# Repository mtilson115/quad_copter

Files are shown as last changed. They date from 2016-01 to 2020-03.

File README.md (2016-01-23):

quad_copter
===========

Microchip PIC32MX795F512L With uCOS RTOS and Accel Gyro driver port from arduino

**Compiling**

1. Install the xc32 compiler from microchip
2. Modify Makefile to point CC to the to where the compiler is located
3. type make

**Output Files**

A binary (same as a .elf) and a .hex file will be placed in the BIN directory

**Modifying what is included in the build**

In side Makefile, you can modify the DIRS variable to include new folders to compile.

**Required directory structure**

If you do add new folders to the build, you must use the ./src and ./inc file naming structure for the
build system to work.

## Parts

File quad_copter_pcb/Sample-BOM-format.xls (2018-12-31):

This is a sample BOM for online BOM pricing system. Please use this preferred format for your BOM that you upload.
Note: DNI applies to whole row. If only some specific locations of a given ITEM are not to be installed, please create two rows for that item and mark one as DNI.
BOM: <Board Name Here>
Assembly Part Number/Revision:
Customer / Company Name:
Item # | Quantity per board | Manufacturer Part # | Do Not Install | Reference designators | Vendor (optional) | Vendor Part Number (optional) | Value (optional) | Size / Footprint (optional) | Part description/ specs (optional, but recommended) | Manfacturer (optional)
1 | 58 | ECJ-0EB1E103K |  | C1,C2,C3,C4,C5,C6,C7,C8,C9,C10,C21,C22,C23,C24,C25,C26,C33,C34,C35,C36,C37,C38,C39,C40,C41,C42,C43,C44,C45,C46,C47,C48,C69,C70,C71,C72,C73,C74,C75,C76,C77,C78,C79,C80,C81,C82,C83,C84,C85,C86,C87,C88,C89,C90,C91,C92,C121,C122 | Digi-Key | PCC2270CT-ND | 0.01uF | C0402 | CAP .01UF 25V CERAMIC X7R 0402 | Panasonic
2 | 2 | T520L337M2R5ATE025 |  | C12,C15 | Digi-Key | 399-5134-1-ND | 330uF | C6032 | CAP TANT 330UF 2.5V 20% SMD | Kemet
3 | 2 | T520L337M2R5ATE025 | DNI | C16,C17 | Digi-Key | 399-5134-1-ND | 330uF | C6032 | CAP TANT 330UF 2.5V 20% SMD | Kemet
4 | 6 | ECJ-2FB1E475M |  | C29,C30,C31,C32,C59,C60 | Digi-Key | PCC2321CT-ND | 4.7uF | C0805 | CAP CERAMIC 4.7UF 25V X5R 0805 | Panasonic
5 | 32 | GRM155F51E104ZA01D |  | C61,C62,C63,C64,C93,C94,C95,C96,C97,C98,C99,C100,C101,C102,C103,C104,C105,C106,C107,C108,C109,C110,C111,C112,C113,C114,C115,C116,C125,C126,C127,C128 | Digi-Key | 490-3271-1-ND | 0.1uF | C0402 | CAP CER .1UF 25V Y5V 0402 | Murata
6 | 10 | C3225X7R1E106M | DNI | C65,C66,C67,C68,C119,C120, C147,C158,C170,C171 | Mouser | 810-C3225X7R1E106M | 10uF | C1210 (3225 metric) | CAP CER 10uF 25V X7R 20% SMD 1210 | TDK
7 | 2 | ECJ-2FF1H105Z |  | C146,C156 | Digi-Key | PCC2404CT-ND | 1uF | C0805 | CAP CERAMIC 1UF 50V F 0805 | Panasonic
8 | 3 | C0805C103K5RACTU |  | C149,C151,C161 | Digi-Key | 399-1158-1-ND | 10nF | C0805 | CAP 10000PF 50V CERAMIC X7R 0805 | KEMET
9 | 3 | LMK325BJ476MM-T |  | C167, C169, C141 | Digi-Key | 587-1383-1-ND | 47uF | C1210 (3225 metric) | CAP CER 47UF 10V X5R 1210 | Taiyo Yuden
10 | 3 | C3216X5R1A106M |  | C139,C142,C174 | Digi-Key | 445-1387-1-ND | 10uF | C1206 (3216 metric) | CAP CER 10UF 10V X5R 20% 1206 | Panasonic
11 | 5 | CC0805KRX7R9BB104 |  | C159, C152, C162, C166, C168 | Digi-Key | 311-1140-1-ND | 0.1uF | C0805 | CAP .10UF 50V CERAMIC X7R 0805 | Yageo
12 | 1 | T495D477M006ATE045 |  | C153 | Digi-Key | 399-5220-1-ND | 470uF | C7343-31 | CAP TANTALUM 470UF 6.3V 0.045ohm ESR SMD | Kemet
13 | 5 | ECJ-2VB1H102K |  | C154,C148,C157,C160,C150 | Digi-Key | PCC102BNCT-ND | 1000pF | c0805 | CAP 1000pF 50V CERAMIC X7R 0805 | Panasonic
14 | 2 | C3216X5R0J476M |  | C163,C164 | Digi-Key | 445-1428-1-ND | 47uF | c1206 (3216 metric) | CAP CER 47UF 6.3V X5R 20% 1206 | TDK
15 | 2 | B540C-13-F |  | D1,D2 | Digi-Key | B540C-FDICT-ND | 40V 5A | SMC | DIODE SCHOTTKY 40V 5A SMC | Diodes Inc
16 | 12 | APHCM2012CGCK-F01 |  | D3,D4,D5,D6,D7,D8,D9,D10,D11,D12,D13,D14 | Digi-Key | 754-1094-1-ND | LED | LED0805 | LED 2X1.25MM LOPRO 570NM GRN SMD | Kingbright Corp
17 | 2 | 12226-8250-00FR | DNI | J1,J4 | Mouser | 517-12226-825000FR | 12226-8250-00FR | CONN_SMD-26 | CONN SDR 26POS R/A RECEPT SMD | 3M
18 | 1 | 141-0701-201 |  | J2 | Mouser | 530-141-0701-201 | SMA-VERT | CON_SMA_V_TH | SMA Connector STR PC MNT JACK RECPT STAINLESS STEEL | Emerson
19 | 1 | 2-5177986-5 |  | J5 | Digi-Key | A35089CT-ND | CON120 | conn_2x60_th | CONN PLUG 120 POS VERT DUAL | TE Connectivity
20 | 6 | 961103-6404-AR |  | J6,J7,J8,J9,J15,J17 | Digi-Key | 3M9448-ND | CON3 | HDR1X3_TH | CONN HEADER VERT SGL 3POS GOLD | 3M
21 | 1 | 87831-1420 |  | J10 | Digi-Key | WM17469-ND | 87831-1420 | conn_2x7th | CONN HEADER 14POS 2MM VERT GOLD | Molex
22 | 2 | ASP-134488-01 |  | J11,J12 | Samtec Inc | ASP-134488-01 | ASP-134488-01 | SMD_50x8_BGA | CONN SNGL-END ARRAY MALE 400POS | Samtec Inc
23 | 1 | 961102-6404-AR |  | J16 | Digi-Key | 3M9447-ND | JUMPER | HDR1X2TH | CONN HEADER VERT SGL 2POS GOLD | 3M
24 | 25 | GBC36SFBN-M30 |  | JP1-JP25 | Digi-Key | S1043E-36-ND | 1 PIN HEADER | HDR1x1 | 1 PIN HEADER; BREAK FROM 36 PIN STANDARD HEADER STRIP | Sullins
25 | 3 | MPZ2012S601A |  | L1,L2,L3 | Digi-Key | 445-2206-1-ND | INDUCTOR | ind_0805 | FERRITE CHIP BEAD 600 OHM SMD | TDK
26 | 3 | MSS1048-103MLB |  | L4,L6,L7 | COILCRAFT | MSS1048-103MLB | 10uH | ind_Mss1048 | INDUCTOR POWER 10UH 4.0A SMD 26mOHM | COILCRAFT
27 | 1 | SRR1260-120M |  | L5 | Arrow | SRR1260-120M | 12uH | ind_Srr1260 | INDUCTOR POWER 12UH 5.0A SMD 23mOHM | BOURNS
28 | 1 | SRR6603-1R5ML |  | L8 | Digi-Key | SRR6603-1R5MLCT-ND | 1.5uH | ind_Srr6603 | INDUCTOR POWER 1.5UH 2.8A SMD 45mOHM | BOURNS
29 | 6 | ERJ-2GEJ271X |  | R1,R2,R3,R4,R5,R6 | Digi-Key | P270JCT-ND | 270R | R0402 | RES 270 OHM 1/10W 5% 0402 SMD | Panasonic
30 | 3 | ERJ-2GEJ331X |  | R7,R8,R9 | Digi-Key | P330JCT-ND | 330 | R0402 | RES 330 OHM 1/10W 5% 0402 SMD | Panasonic
31 | 7 | ERJ-2GEJ472X |  | R10,R11,R21,R22,R23,R24,R25 | Digi-Key | P4.7KJCT-ND | 4.7K | R0402 | RES 4.7K OHM 1/10W 5% 0402 SMD | Panasonic
32 | 12 | RC0402JR-0710KL |  | R26,R27,R28,R42,R43,R44, R50,R51,R52,R53,R54,R55 | Digi-Key | 311-10KJRCT-ND | 10K | R0402 | RES 10K OHM 1/16W 5% 0402 SMD | Panasonic
33 | 2 | ERJ-6ENF6192V |  | R12,R15 | Digi-Key | P61.9KCCT-ND | 61.9K | R0805 | RES 61.9K OHM 1/8W 1% 0805 SMD | Panasonic
34 | 1 | ERJ-6ENF1581V |  | R13 | Digi-Key | P1.58KCCT-ND | 1.58K | R0805 | RES 1.58K OHM 1/8W 1% 0805 SMD | Panasonic
35 | 7 | ERJ-6ENF1001V |  | R14,R17,R20,R34,R35,R36,R40 | Digi-Key | P1.00KCCT-ND | 1K | R0805 | RES 1.00K OHM 1/8W 1% 0805 SMD | Panasonic
36 | 1 | ERJ-6ENF2871V |  | R16 | Digi-Key | P2.87KCCT-ND | 2.87K | R0805 | RES 2.87K OHM 1/8W 1% 0805 SMD | Panasonic
37 | 1 | ERJ-6ENF2492V | DNI | R18 | Digi-Key | P24.9KCCT-ND | 24.9K | R0805 | RES 24.9K OHM 1/8W 1% 0805 SMD | Panasonic
38 | 1 | ERJ-6ENF2550V |  | R19 | Digi-Key | P255CCT-ND | 255 | R0805 | RES 255 OHM 1/8W 1% 0805 SMD | Panasonic
39 | 7 | RC0603JR-07100RL |  | R29,R30,R31,R32,R33,R48,R49 | Digi-Key | 311-100GRCT-ND | 100 | R0603 | RES 100 OHM 1/10W 5% 0603 SMD | Panasonic
40 | 4 | ERJ-3GEY0R00V |  | R37,R45,R46,R47 | Digi-Key | P0.0GCT-ND | 0 | R0603 | RES ZERO OHM 1/10W 5% 0603 SMD | Panasonic
41 | 2 | PTS645VL31 LFS |  | SW1,SW2 | Digi-Key | CKN9094-ND | PTS645VL31 LFS | sw_tact_6mm_th | SWITCH TACT R/A 6MM H=3.15MM, Through Hole, Right Angle | C&K Components
42 | 2 | SN74ALVC244NSR |  | U1,U7 | Digi-Key | 296-12863-1-ND | SN74ALVC244 | SOP-20 | IC BUFF/DVR TRI-ST OCTAL 20SOP | Texas Instruments
43 | 2 | XCF32PVOG48C |  | U2,U8 | Digi-Key | 122-1458-ND | XCF32PVOG48C | TSOP-48 | IC PROM SRL 1.8V 32M GATE 48TSOP | Xilinx
44 | 2 | XC5VLX110-3FFG1760C |  | U3,U6 | Nu Horizons | XC5VLX110-3FFG1760C | XC5VLX110-3FFG1760C | BGA-1760 | IC FPGA VIRTEX-5 110K 1760FBGA | Xilinx
45 | 2 | LM22670TJE-ADJ/NOPB |  | U4,U5 | Digi-Key | LM22670TJE-ADJCT-ND | LM22670TJE-ADJ/NOPB | TO263-7 | IC REG SWITCH BUC 3A ADJ TO263-7 | Texas Instruments
46 | 2 | LM3102MH/NOPB |  | U9,U11 | Newark | 54M4671 | LM3102MH/NOPB | TSSOP-20 | IC REG SYNC BUCK 42V2.5A 20TSSOP | Texas Instruments
47 | 1 | SN65LVDS179DGK | DNI | U13 | Digi-Key | 296-6918-5-ND | SN65LVDS179DGK | MSOP-8 | IC HS DIFF LINE DRVR/RCVR 8-MSOP | Texas Instruments
48 | 1 | CSX750FBC-20.000M-UT |  | U14 | Mouser | 695-CSX750FBC-20 | CSX-750FBC-20Mhz | OSC_CSX750 | OSC 3.3V PROG CMOS OE 100PPM 20MHZ | Citizen
END OF BOM

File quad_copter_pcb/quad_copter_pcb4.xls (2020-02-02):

This is a sample BOM for online BOM pricing system. Please use this preferred format for your BOM that you upload.
Note: DNI applies to whole row. If only some specific locations of a given ITEM are not to be installed, please create two rows for that item and mark one as DNI.
BOM: Quad Copter
Assembly Part Number/Revision: 00000002
Customer / Company Name: Mitchell Tilson
Item # | Quantity per board | Manufacturer Part # | Do Not Install | Reference designators | Vendor (optional) | Vendor Part Number (optional) | Value (optional) | Size / Footprint (optional) | Part description/ specs (optional, but recommended) | Manfacturer (optional)
1 | 1 | CL21A106KOQNNNE |  | C1 | Digi-Key | 1276-1096-2-ND | 10uF | c0805 | CAP CER 10UF 16V X5R 0805 | Samsung Electro-Mechanics
2 | 1 | TAJA226M010RNJ |  | C2 | Digi-Key | 478-5798-1-ND | 22uF | c1206 | 22µF Molded Tantalum Capacitors 10V 1206 (3216 Metric) 3 Ohm | AVX
3 | 2 | 06031A250GAT2A |  | C4,C5 | Digi-Key | 478-10197-2-ND | 26pF | c0603 | 25pF ±2% 100V Ceramic Capacitor C0G, NP0 0603 (1608 Metric) | AVX
4 | 7 | CL10F104ZO8NNNC |  | C9,C10,C8,C7,C11,C13,C12 | Digi-Key | 1276-1258-6-ND | 0.1uF | c0603 | CAP CER 0.1UF 16V Y5V 0603 | Samsung Electro-Mechanics
5 | 1 | CL10A106MQ8NNNC |  | C6 | Digi-Key | 1276-1119-1-ND | 10uF | c0603 | CAP CER 10UF 6.3V X5R 0603 | Samsung Electro-Mechanics
6 | 2 | 06033A150JAT2A |  | C14,C15 | Digi-Key | 478-10804-2-ND | 15pF | c0603 | CAP CER 15PF 25V C0G/NP0 0603 | AVX
7 | 3 | SML-LX1206GW-TR |  | D3,D2,D1 | Digi-Key | 67-1002-1-ND |  | led1206 | LED GREEN DIFFUSED 1206 SMD | Lumex Opto/Components Inc.
8 | 1 | 10103594-0001LF |  | J12 | Digi-Key | 609-4050-1-ND |  |  | CONN RCPT USB2.0 MICRO B SMD R/A | Amphenol FCI
9 | 1 | 317-87-121-41-005101 |  | JP2 | Digi-Key | 1212-1133-ND |  | pitch: 0.070" (1.78mm) | PCB SKT, 21 POLE | Preci-Dip
10 | 1 | RJ11-6N-B |  | JP1 | Digi-Key | CCM1394-ND |  |  | CONN MOD JACK 6P6C R/A UNSHLD | TE Connectivity Corcom Filters
11 | 3 | RR1220P-103-D |  | R4,R6,R2 | Digi-Key | RR12P10.0KDTR-ND | 10k | r0805 | RES SMD 10K OHM 0.5% 1/10W 0805 | Susumu
12 | 3 | RMCF0805JT56R0 |  | R9,R8,R1 | Digi-Key | RMCF0805JT56R0DKR-ND | 56 | r0805 | RES 56 OHM 5% 1/8W 0805 | Stackpole Electronics Inc.
13 | 2 | CR0603-JW-471ELF |  | R5,R7 | Digi-Key | CR0603-JW-471ELFCT-ND | 470 | r0603 | RES SMD 470 OHM 5% 1/10W 0603 | Bourns Inc.
14 | 1 | RC0805FR-072K8L |  | R3 | Digi-Key | 311-2.80KCRTR-ND | 2.8k | r0805 | RES SMD 2.8K OHM 1% 1/8W 0805 | Yageo
15 | 2 | RR1220P-242-D |  | R12,R13 | Digi-Key | RR12P2.4KDTR-ND | 2.4k | r0805 | RES SMD 2.4K OHM 0.5% 1/10W 0805 | Susumu
16 | 1 | RNCS0805BKE10R0 |  | R14 | Digi-Key | RNCS0805BKE10R0TR-ND | 10 | r0805 | RES 10 OHM 0.1% 1/10W 0805 | Stackpole Electronics Inc.
17 | 2 | RS-187R05A2-DS MT RT |  | S1,S2 | Digi-Key | CKN10361TR-ND |  | TACTILE_SWITCH_SMD_5.2MM | SWITCH TACTILE SPST-NO 0.05A 12V | C&K
18 | 1 | PIC32MX795F512L-80I/PT |  | U4 | Digi-Key | PIC32MX795F512L-80I/PT-ND |  | TQFP-100_12x12mm_P0.4mm | IC MCU 32BIT 512KB FLASH 100TQFP | Microchip Technology
19 | 1 | LT1085CM-3.3#PBF |  | U1 | Digi-Key | LT1085CM-3.3#PBF-ND | 3.3V |  | IC REG LINEAR 3.3V 3A D2PAK-3 | Linear Technology/Analog Devices
20 | 1 | PPTC081LFBN-RC |  | U3 | Digi-Key | S7006-ND | CONN8 | .1’’ pitch | CONN HEADER FEMALE 8POS .1" TIN | Sullins Connector Solutions
21 | 1 | CM200C32768HZFT |  | Y2 | Digi-Key | 300-8742-1-ND | 32kHz | Crystal_SMD_7050-4Pin_7.0x5.0mm | CRYSTAL 32.7680KHZ 12.5PF SMD | Citizen Finedevice Co Ltd
22 | 1 | 9C-8.000MEEJ-T |  | Y1 | Digi-Key | 887-1263-2-ND | 8MHz | HC49UP | CRYSTAL 8.0000MHZ 18PF SMD | TXC CORPORATION
END OF BOM

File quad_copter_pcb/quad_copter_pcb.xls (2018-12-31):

Title | Quad Copter
Revision | 1
Date | Sat 08 Dec 2018 03:06:19 PM PST
Generated | Sat 08 Dec 2018 03:06:19 PM PST
Company | Self
Comment 1
Comment 2
Comment 3
Comment 4
Total Parts | 64
Total Unique Parts | 32
Ref | Qty | Value | Footprint | Field4 | Part Reference | Notes
C1 | 1 | C_10uF | Capacitor_SMD:C_0805_2012Metric_Pad1.15x1.40mm_HandSolder |  | https://www.digikey.com/product-detail/en/tdk-corporation/C2012JB1V106M085AC/445-11518-6-ND/3957614 | Please order and solder in
C2 | 1 | C_22uF | Capacitor_SMD:C_1206_3216Metric_Pad1.42x1.75mm_HandSolder |  | https://www.digikey.com/product-detail/en/avx-corporation/TAJA226M010RNJ/478-5798-1-ND/2136389 | Please order and solder in
C5 C4 | 2 | C26pF | Capacitor_SMD:C_0603_1608Metric_Pad1.05x0.95mm_HandSolder |  | https://www.digikey.com/product-detail/en/avx-corporation/06031A250GAT2A/478-10197-2-ND/1598435 | Please order and solder in
C9 C10 | 2 | C_.1uF | Capacitor_SMD:C_0603_1608Metric_Pad1.05x0.95mm_HandSolder |  | https://www.digikey.com/product-detail/en/samsung-electro-mechanics/CL10F104ZO8NNNC/1276-1258-6-ND/3891772 | Please order and solder in
C6 | 1 | C10uF | Capacitor_SMD:C_0603_1608Metric_Pad1.05x0.95mm_HandSolder |  | https://www.digikey.com/product-detail/en/tdk-corporation/C1608X5R0J106M080AB/445-4112-2-ND/1975459 | Please order and solder in
C8 C7 C11 C13 C12 | 5 | C.1uF | Capacitor_SMD:C_0603_1608Metric_Pad1.05x0.95mm_HandSolder |  | https://www.digikey.com/product-detail/en/samsung-electro-mechanics/CL10F104ZO8NNNC/1276-1258-6-ND/3891772 | Please order and solder in
C15 C14 | 2 | C15pF | Capacitor_SMD:C_0603_1608Metric_Pad1.05x0.95mm_HandSolder |  | https://www.digikey.com/product-detail/en/avx-corporation/06033A150JAT2A/478-10804-2-ND/1599104 | Please order and solder in
D3 D2 D1 | 3 | LED | LED_SMD:LED_1206_3216Metric_Pad1.42x1.75mm_HandSolder |  | https://www.digikey.com/product-detail/en/lumex-opto-components-inc/SML-LXFT1206SGD-TR/SML-LXFT1206SGD-TR-ND/7364535 | Please order and solder in
H1 H2 H3 H4 H5 H6 H7 H8 H9 H10 | 10 | MountingHole_Pad | MountingHole:MountingHole_2.5mm_Pad |  |  | I have this already
H11 H13 H12 H_4 | 4 | MountingHole | MountingHole:MountingHole_3.2mm_M3 |  |  | I have this already
J4 J3 J2 J1 | 4 | Conn_01x03_Male | Connector_PinHeader_2.54mm:PinHeader_1x03_P2.54mm_Vertical |  |  | I have this already
J5 | 1 | Conn_02x05_Odd_Even | Connector_PinHeader_2.54mm:PinHeader_2x05_P2.54mm_Vertical |  |  | I have this already
J6 J9 | 2 | Conn_02x02_Odd_Even | Connector_PinHeader_2.54mm:PinHeader_2x02_P2.54mm_Vertical |  |  | I have this already
J7 J11 | 2 | Conn_01x05 | Connector_PinHeader_2.54mm:PinHeader_1x05_P2.54mm_Vertical |  |  | I have this already
J8 | 1 | Conn_02x04_Odd_Even | Connector_PinHeader_2.54mm:PinHeader_2x04_P2.54mm_Vertical |  |  | I have this already
J12 | 1 | USB_B_Micro | Connector_USB:USB_Micro-B_Amphenol_10103594-0001LF_Horizontal |  | https://www.digikey.com/product-detail/en/amphenol-fci/10103594-0001LF/609-4050-1-ND/2350357 | Please order and solder in
J10 | 1 | Conn_02x03_Odd_Even | Connector_PinHeader_2.54mm:PinHeader_2x03_P2.54mm_Vertical |  |  | I have this already
JP2 | 1 | XBEE LEAVE EMPTY | RF:XBEE | S6B | https://www.digikey.com/product-detail/en/preci-dip/317-87-121-41-005101/1212-1133-ND/3757383 | Please order. I will solder this one in. If part is unavailable, don’t hold up order.
JP1 | 1 | RJ11-6 | Connectors:RJ11-6 | CONN-08590 | https://www.digikey.com/product-detail/en/te-connectivity-corcom-filters/RJ11-6N-B/CCM1394-ND/260247 | Please order and solder in
R4 R6 | 2 | R10k | Resistor_SMD:R_0805_2012Metric_Pad1.15x1.40mm_HandSolder |  | https://www.digikey.com/product-detail/en/susumu/RR1220P-103-D/RR12P10.0KDTR-ND/432315 | Please order and solder in
R9 R8 R1 | 3 | R_56 | Resistor_SMD:R_0805_2012Metric_Pad1.15x1.40mm_HandSolder |  | https://www.digikey.com/product-detail/en/stackpole-electronics-inc/RMCF0805JT56R0/RMCF0805JT56R0DKR-ND/2427421 | Please order and solder in
R5 R7 | 2 | R470 | Resistor_SMD:R_0603_1608Metric_Pad1.05x0.95mm_HandSolder |  | https://www.digikey.com/product-detail/en/bourns-inc/CR0603-JW-471ELF/CR0603-JW-471ELFCT-ND/3740990 | Please order and solder in
R2 | 1 | R10K | Resistor_SMD:R_0805_2012Metric_Pad1.15x1.40mm_HandSolder |  | https://www.digikey.com/product-detail/en/susumu/RR1220P-103-D/RR12P10.0KDTR-ND/432315 | Please order and solder in
R3 | 1 | R2.8k | Resistor_SMD:R_0805_2012Metric_Pad1.15x1.40mm_HandSolder |  | https://www.digikey.com/product-detail/en/yageo/RC0805FR-072K8L/311-2.80KCRTR-ND/727711 | Please order and solder in
R12 R13 | 2 | R2.4k | Resistor_SMD:R_0805_2012Metric_Pad1.15x1.40mm_HandSolder |  | https://www.digikey.com/product-detail/en/susumu/RR1220P-242-D/RR12P2.4KDTR-ND/432300 | Please order and solder in
R14 | 1 | R10 | Resistor_SMD:R_0805_2012Metric_Pad1.15x1.40mm_HandSolder |  | https://www.digikey.com/product-detail/en/stackpole-electronics-inc/RNCS0805BKE10R0/RNCS0805BKE10R0TR-ND/1800064 | Please order and solder in
S1 S2 | 2 | MOMENTARY-SWITCH-SPST-2-SMD-5.2MM | Switches:TACTILE_SWITCH_SMD_5.2MM | SWCH-08247 | https://www.digikey.com/product-detail/en/c-k/RS-187R05A2-DS-MT-RT/CKN10361TR-ND/2747186 | Please order and solder in
U4 | 1 | PIC32MX795F512L-X_PT | Package_QFP:TQFP-100_12x12mm_P0.4mm |  | https://www.microchip.com/wwwproducts/en/PIC32MX795F512L | Please order and solder in. Seriously, I can’t solder this.
U1 | 1 | LT1085-3.3 | Package_TO_SOT_SMD:TO-263-3_TabPin2 |  | http://cds.linear.com/docs/en/datasheet/1083ffe.pdf | Please order and solder in
U3 | 1 | accel_gyro_conn | Connector_PinSocket_2.54mm:PinSocket_1x08_P2.54mm_Vertical |  | https://www.digikey.com/product-detail/en/sullins-connector-solutions/PPTC081LFBN-RC/S7006-ND/810147 | Please order. I will solder this one in.
Y2 | 1 | Crystal_GND23 | Crystal:Crystal_SMD_7050-4Pin_7.0x5.0mm |  | https://www.digikey.com/product-detail/en/citizen-finedevice-co-ltd/CM200C32768HZFT/300-8742-1-ND/2108134 | Please order and solder in
Y1 | 1 | Crystal_8MHz | Clocks:HC49UP |  | https://www.digikey.com/product-detail/en/txc-corporation/9C-8.000MEEJ-T/887-1263-2-ND/2207683 | Please order and solder in
BOM made with KICAD_BOM_WIZARD (https://github.com/HashDefineElectronics/KiCad_BOM_Wizard.git)
Generated Sat 08 Dec 2018 03:06:19 PM PST

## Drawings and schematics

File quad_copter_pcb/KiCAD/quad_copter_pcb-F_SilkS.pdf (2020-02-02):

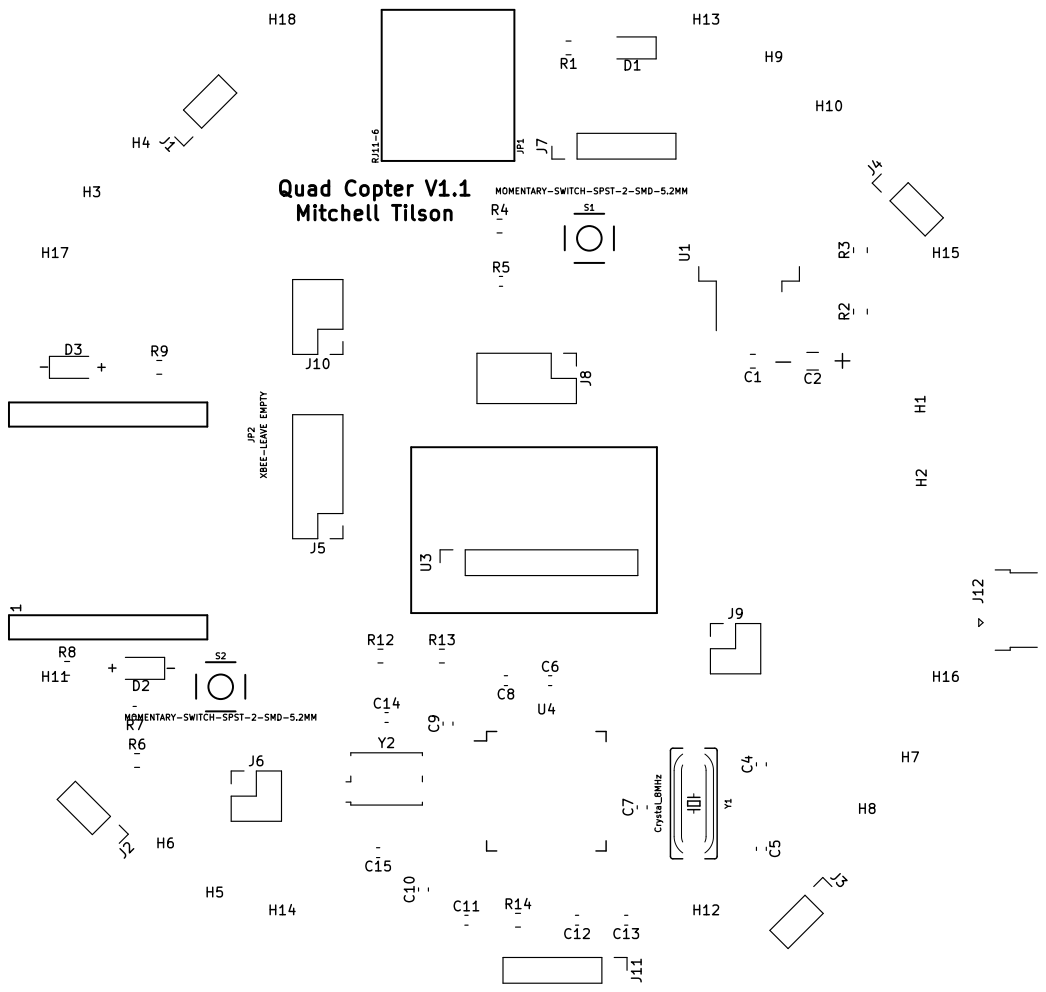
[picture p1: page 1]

Quad Copter V1.1 Mitchell Tilson

S1 MOMENTARY-SWITCH-SPST-2-SMD-5.2MM

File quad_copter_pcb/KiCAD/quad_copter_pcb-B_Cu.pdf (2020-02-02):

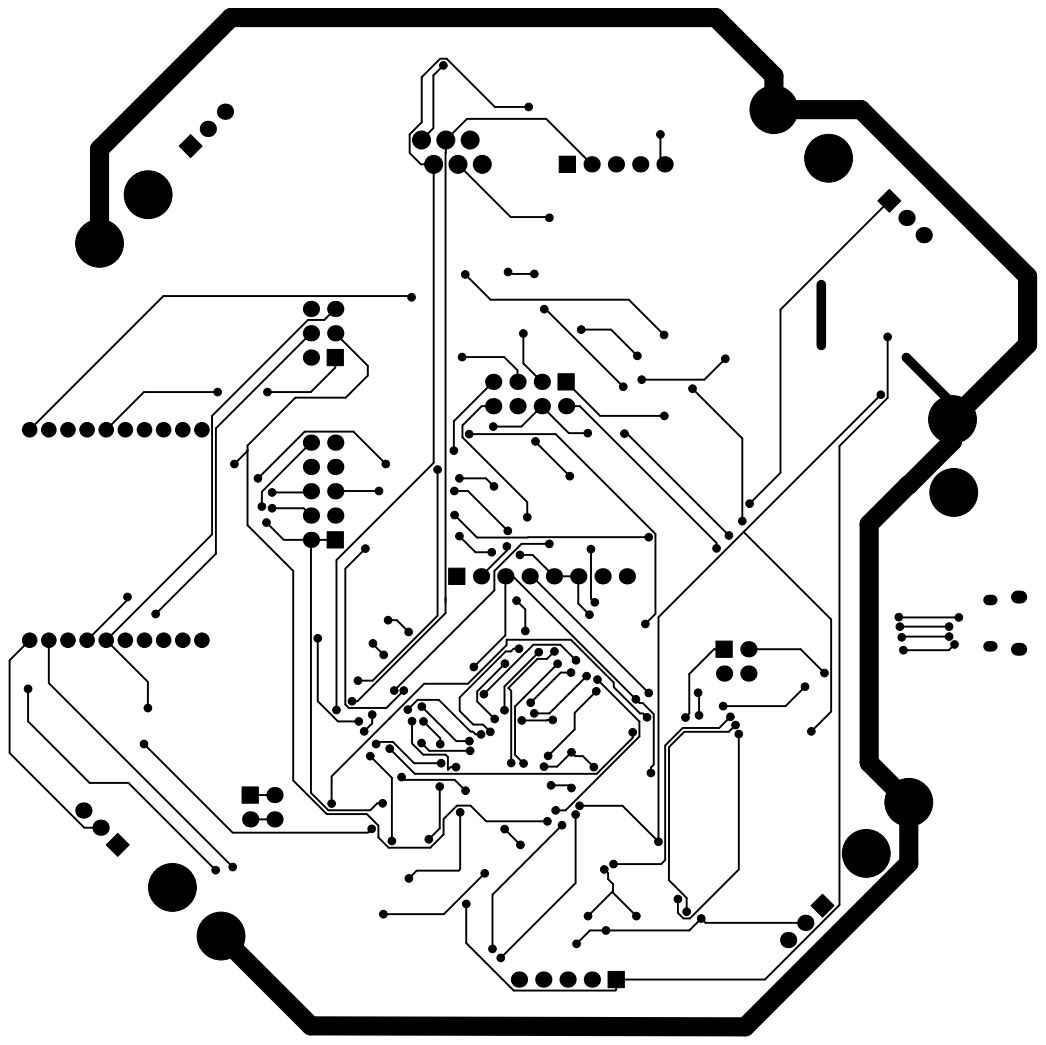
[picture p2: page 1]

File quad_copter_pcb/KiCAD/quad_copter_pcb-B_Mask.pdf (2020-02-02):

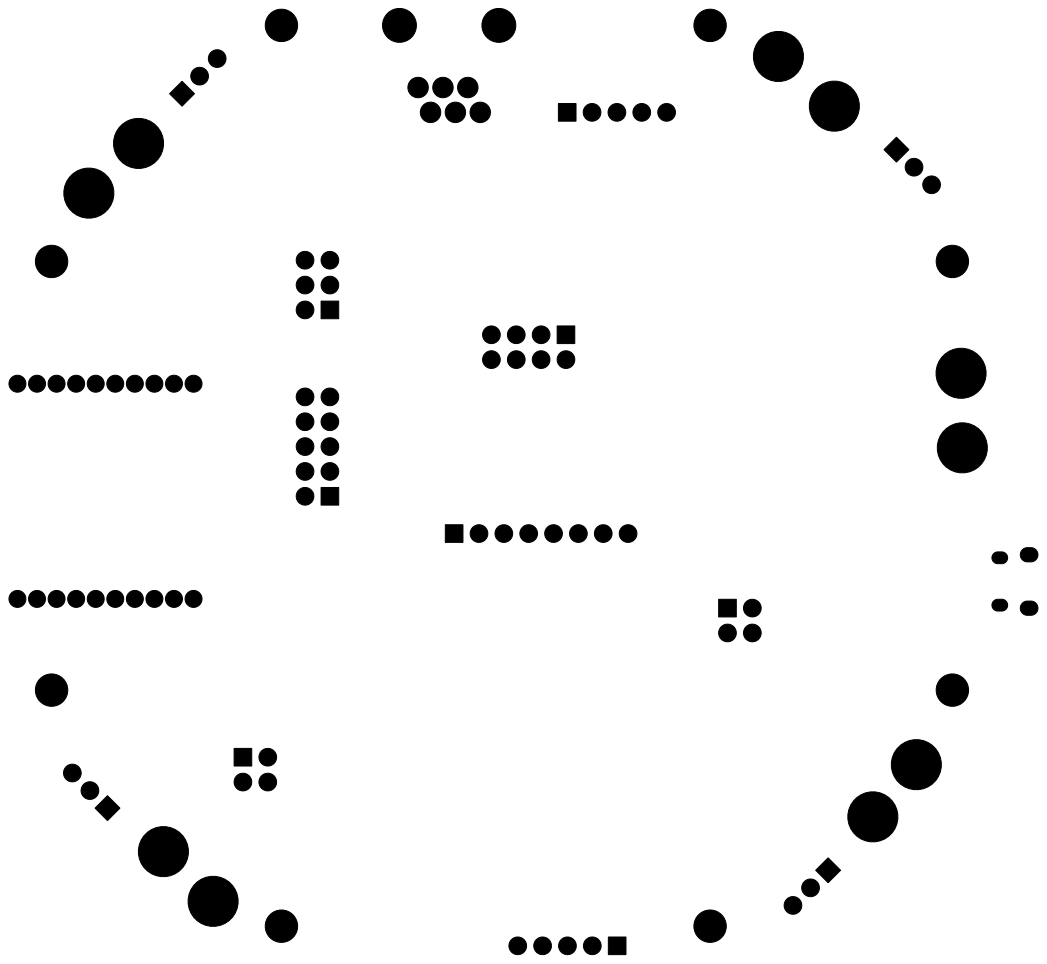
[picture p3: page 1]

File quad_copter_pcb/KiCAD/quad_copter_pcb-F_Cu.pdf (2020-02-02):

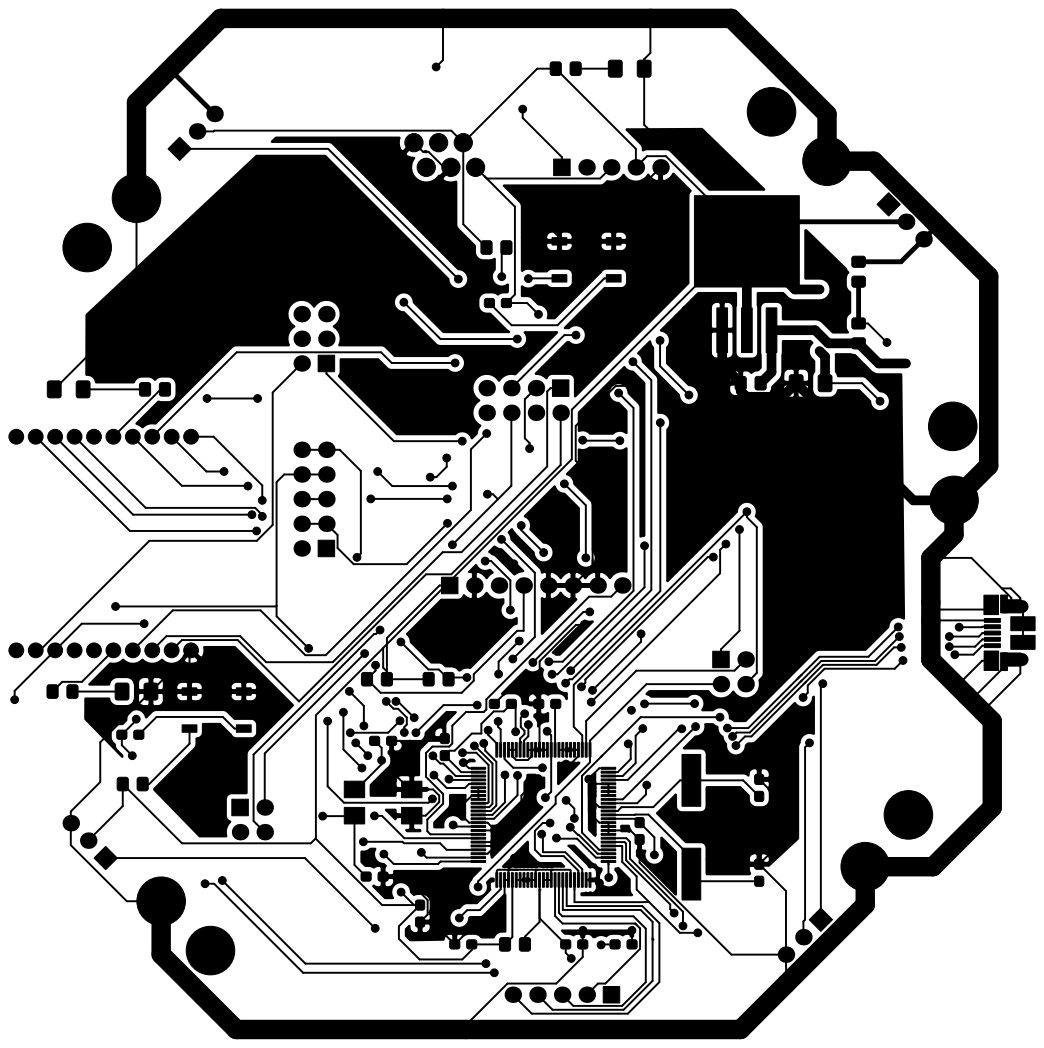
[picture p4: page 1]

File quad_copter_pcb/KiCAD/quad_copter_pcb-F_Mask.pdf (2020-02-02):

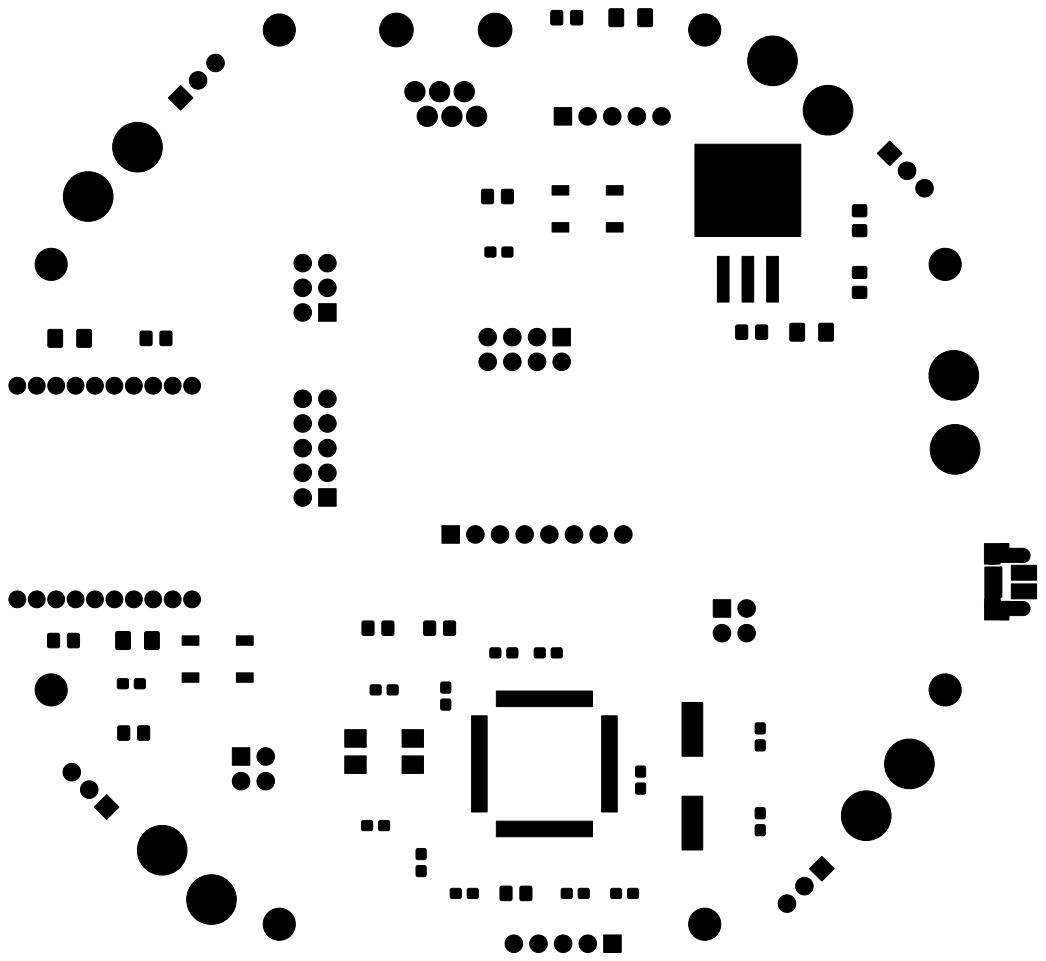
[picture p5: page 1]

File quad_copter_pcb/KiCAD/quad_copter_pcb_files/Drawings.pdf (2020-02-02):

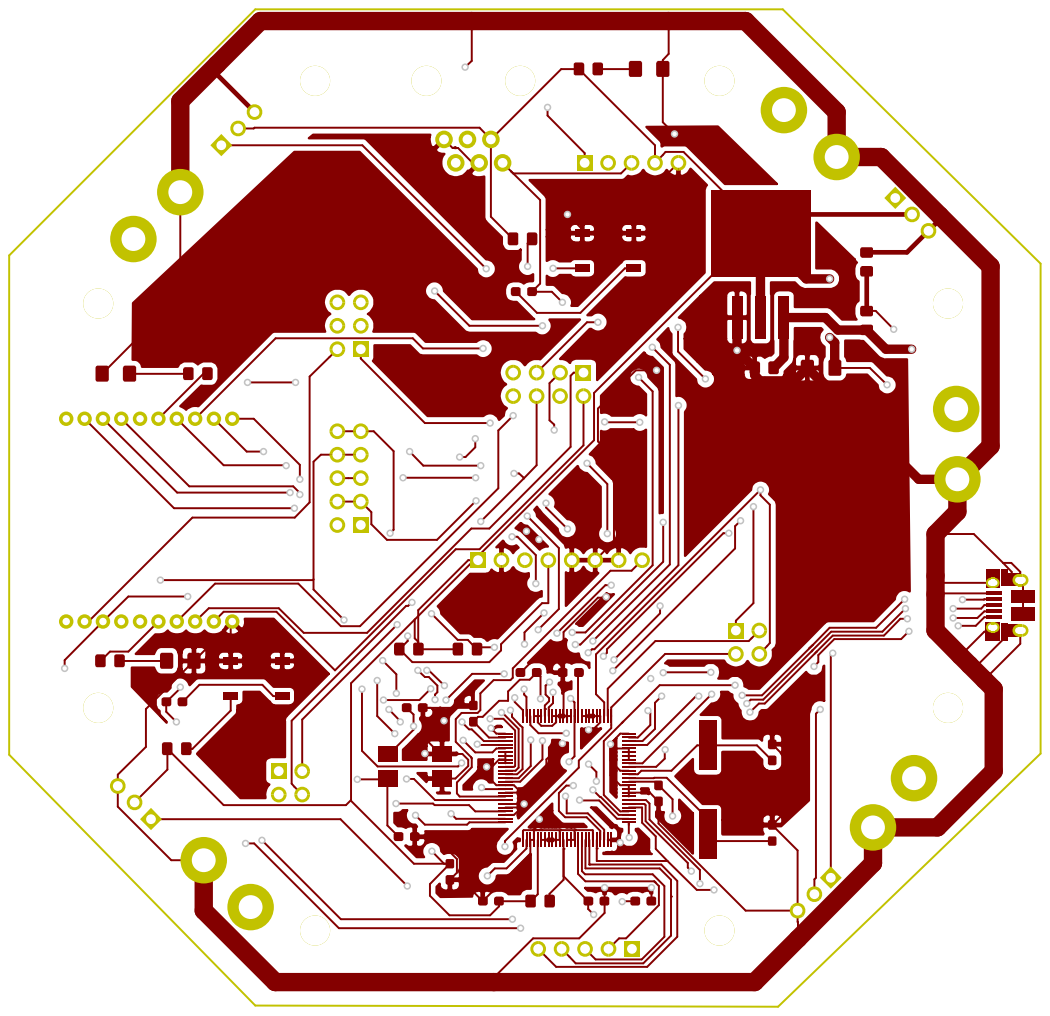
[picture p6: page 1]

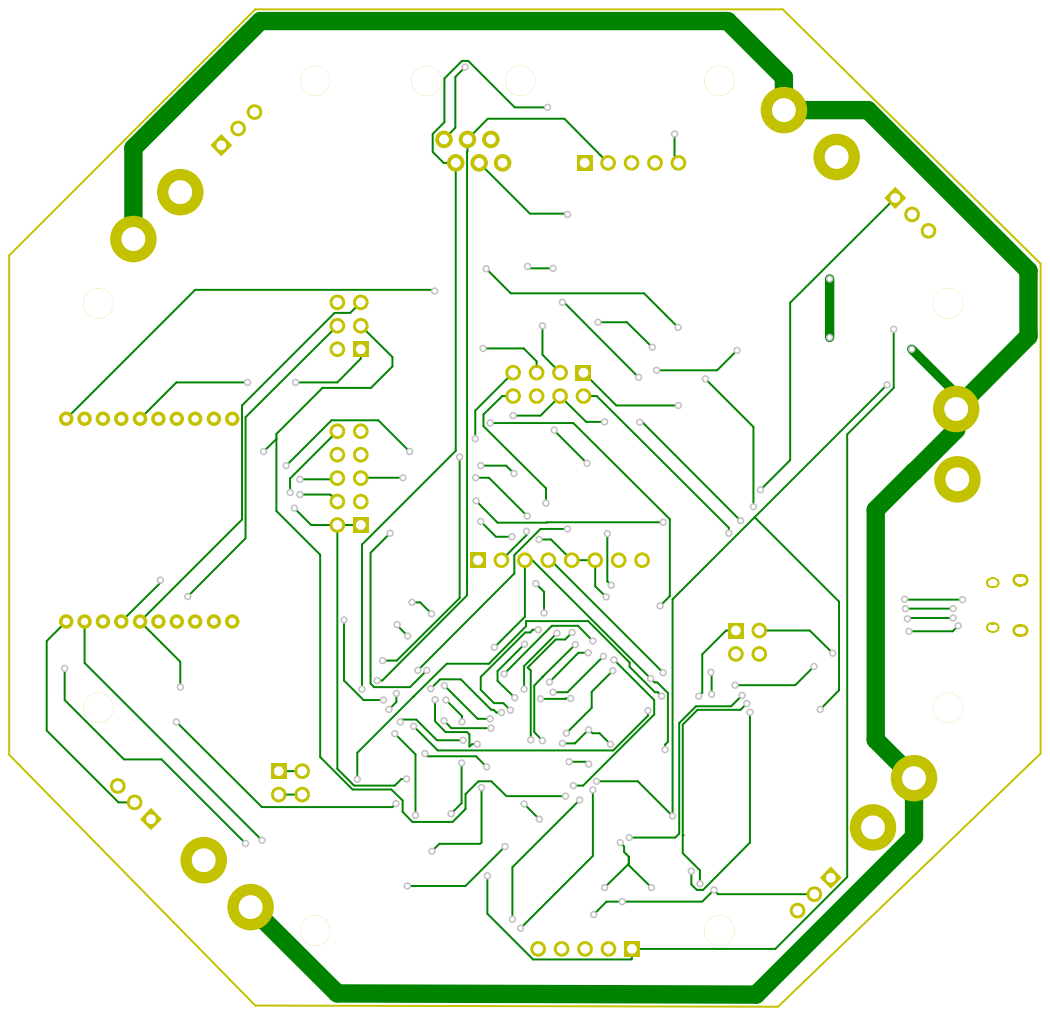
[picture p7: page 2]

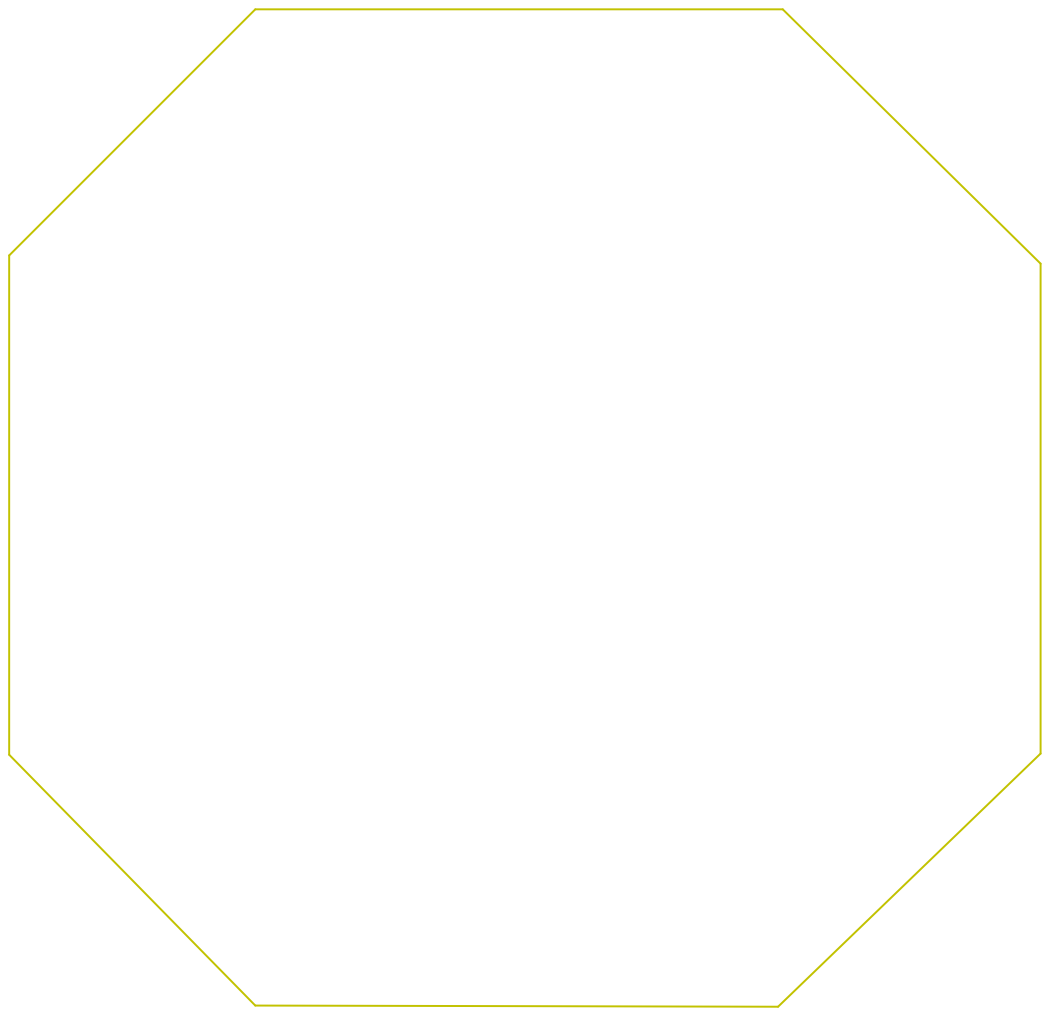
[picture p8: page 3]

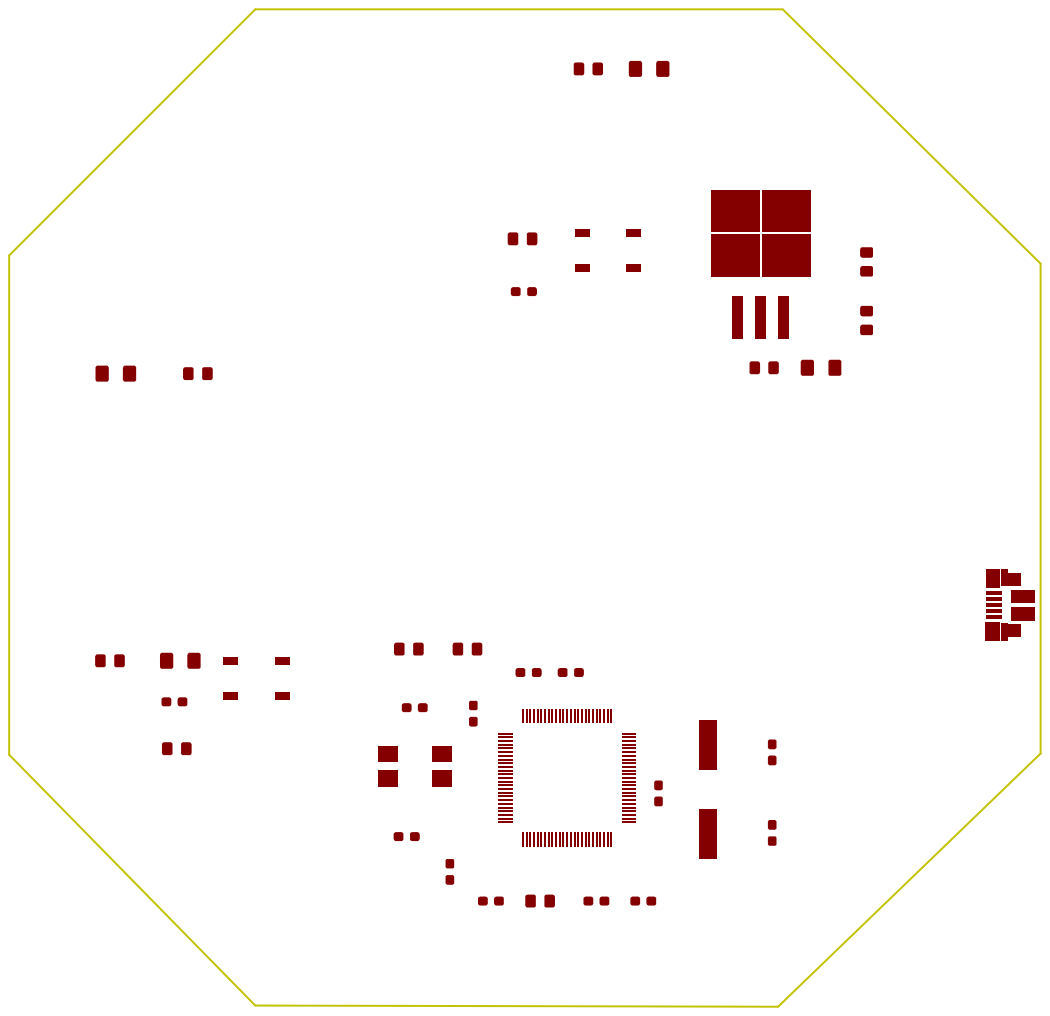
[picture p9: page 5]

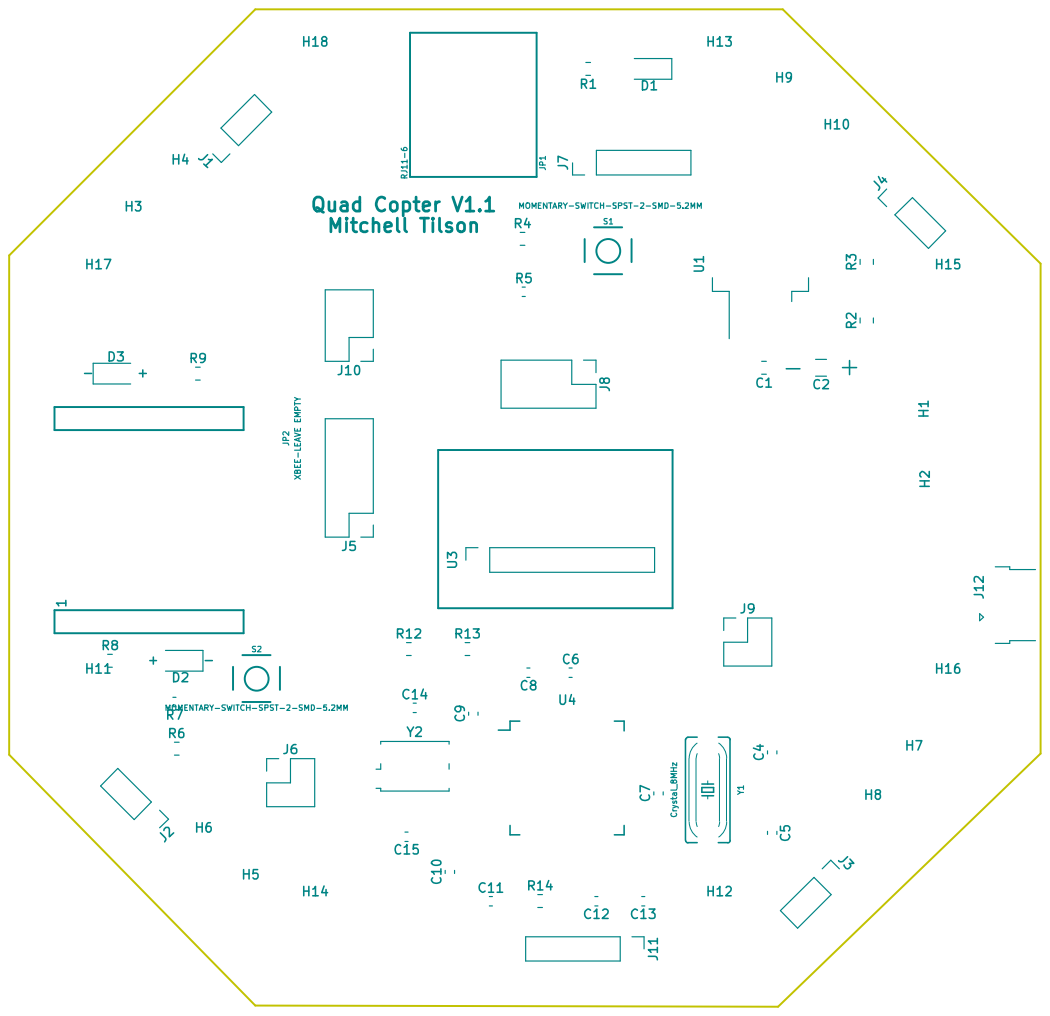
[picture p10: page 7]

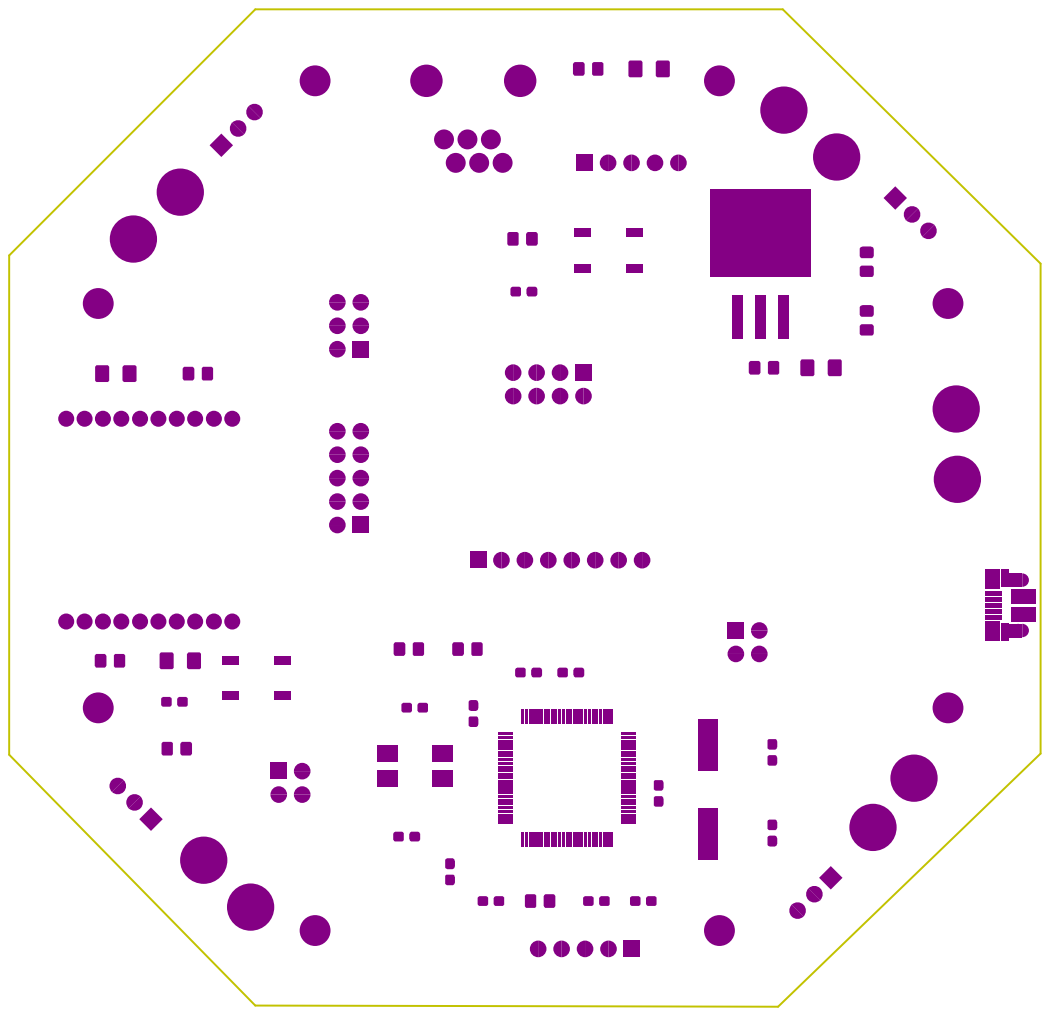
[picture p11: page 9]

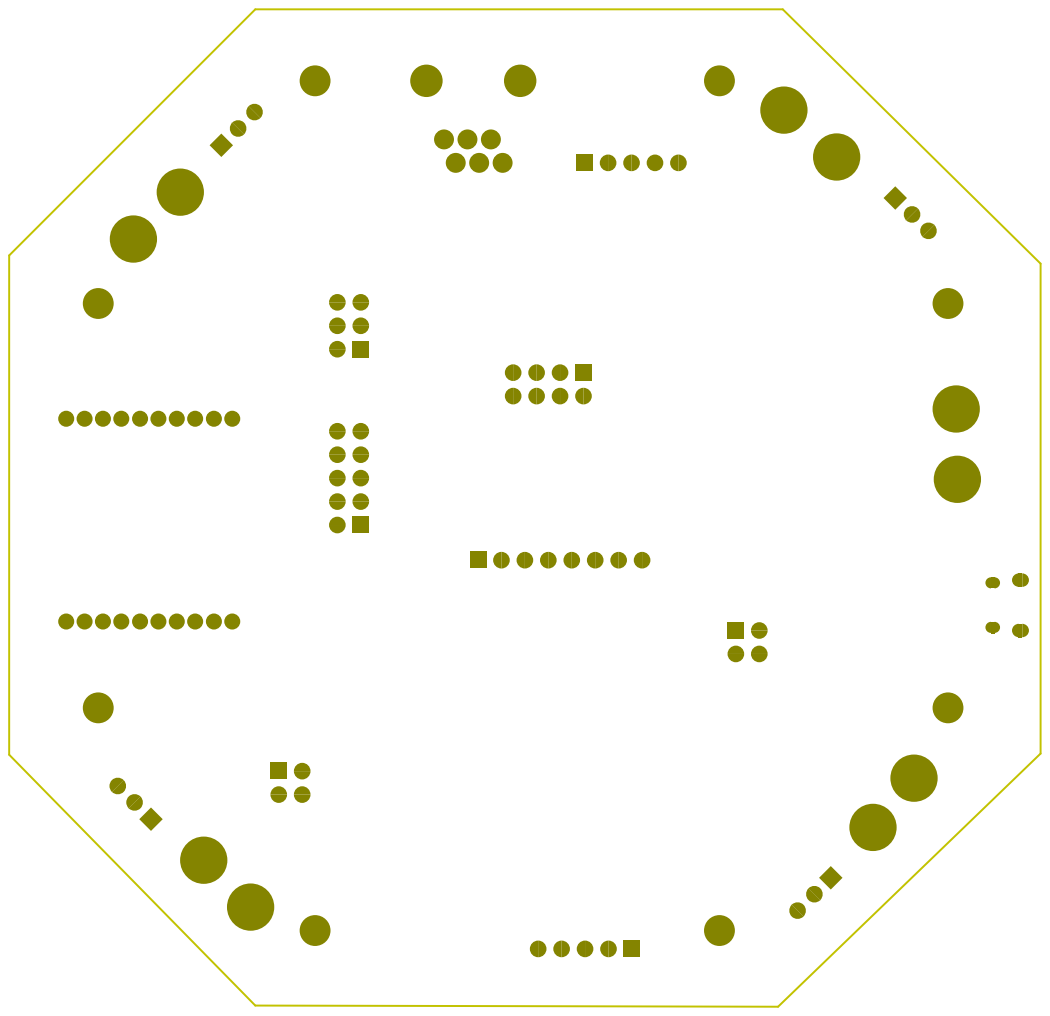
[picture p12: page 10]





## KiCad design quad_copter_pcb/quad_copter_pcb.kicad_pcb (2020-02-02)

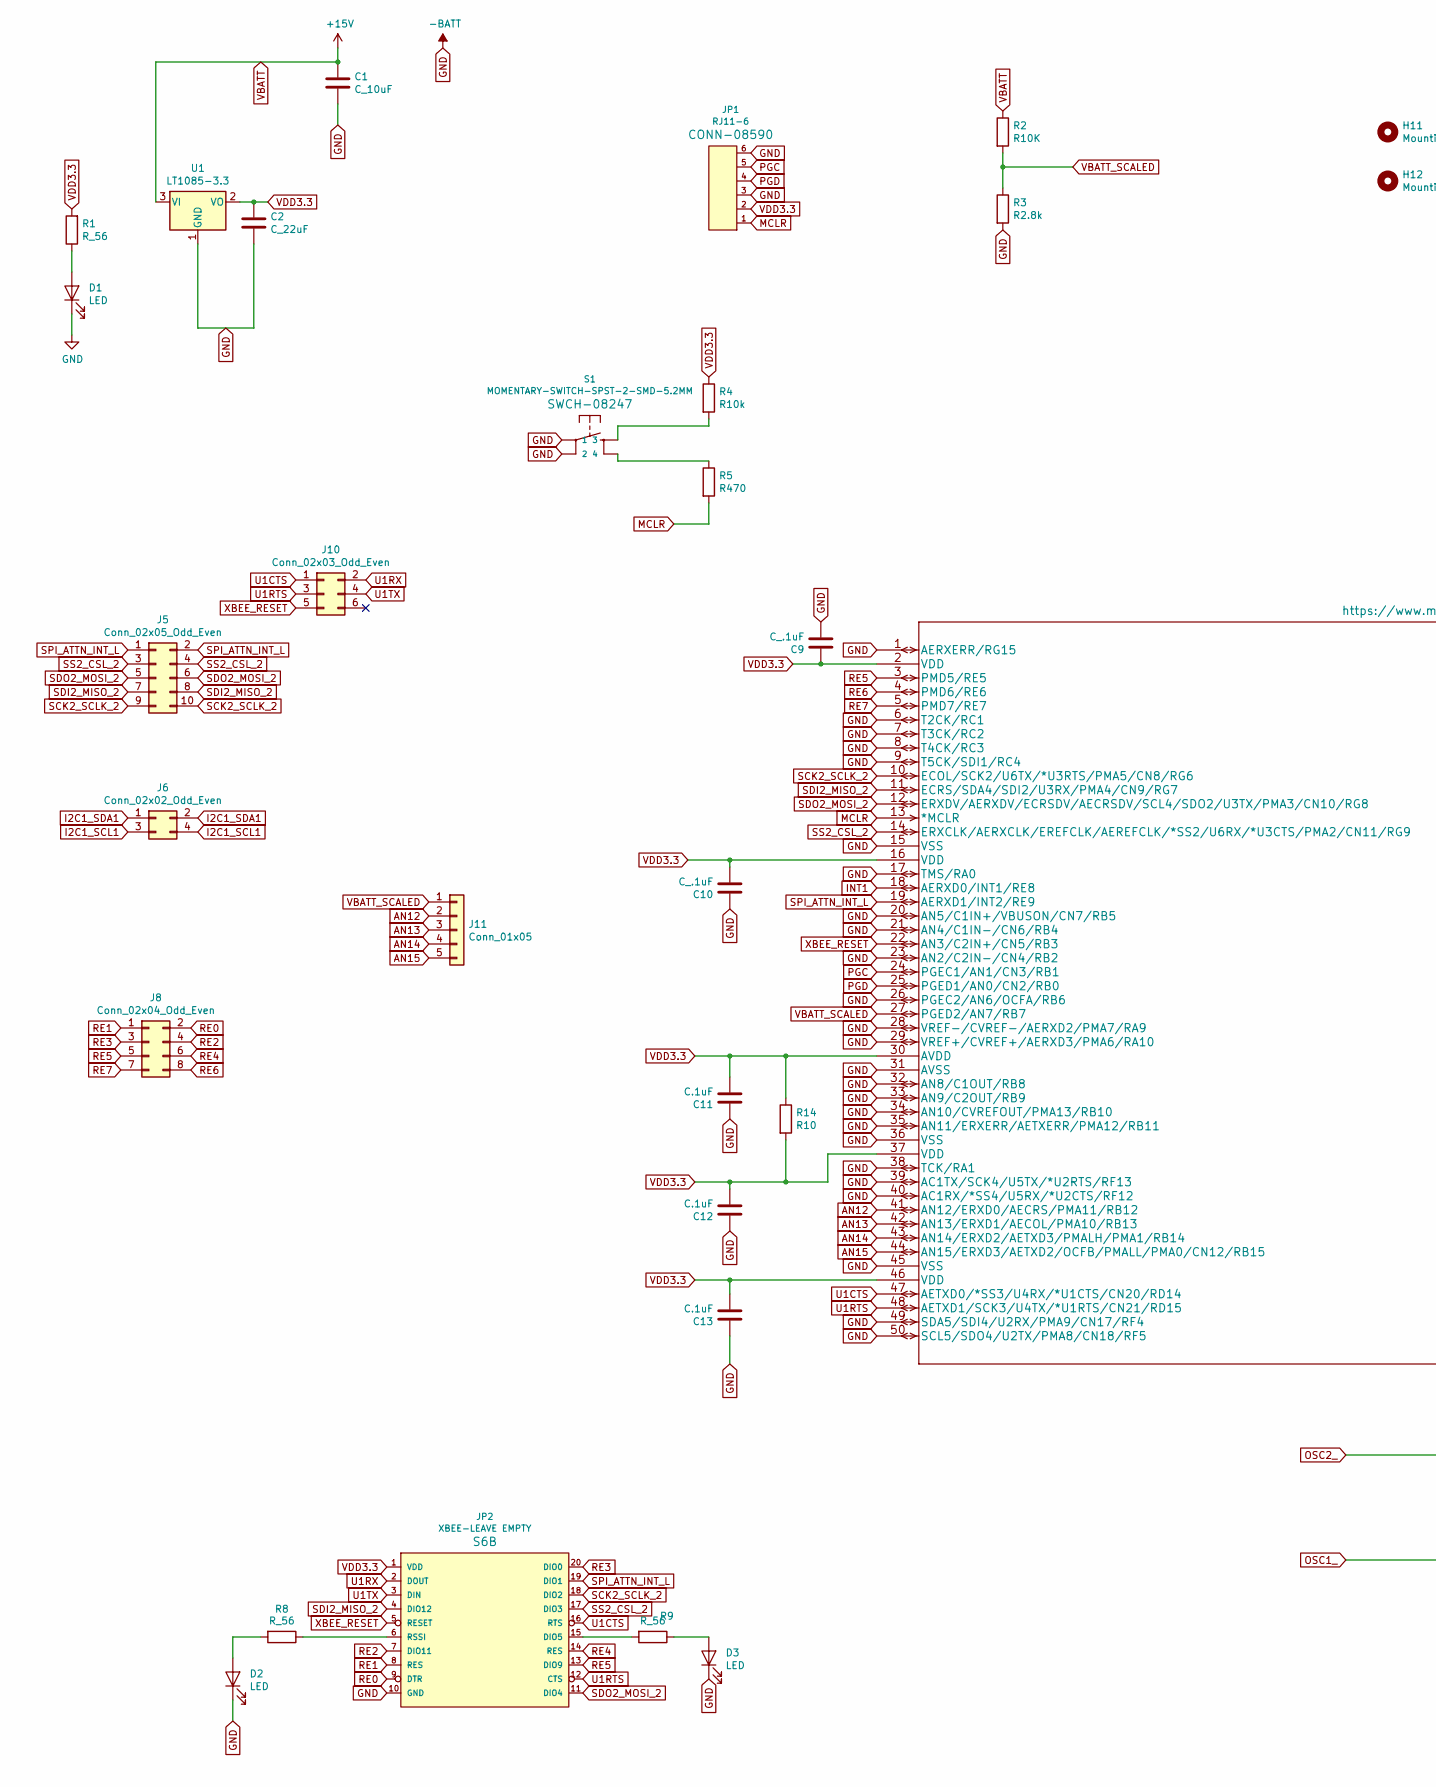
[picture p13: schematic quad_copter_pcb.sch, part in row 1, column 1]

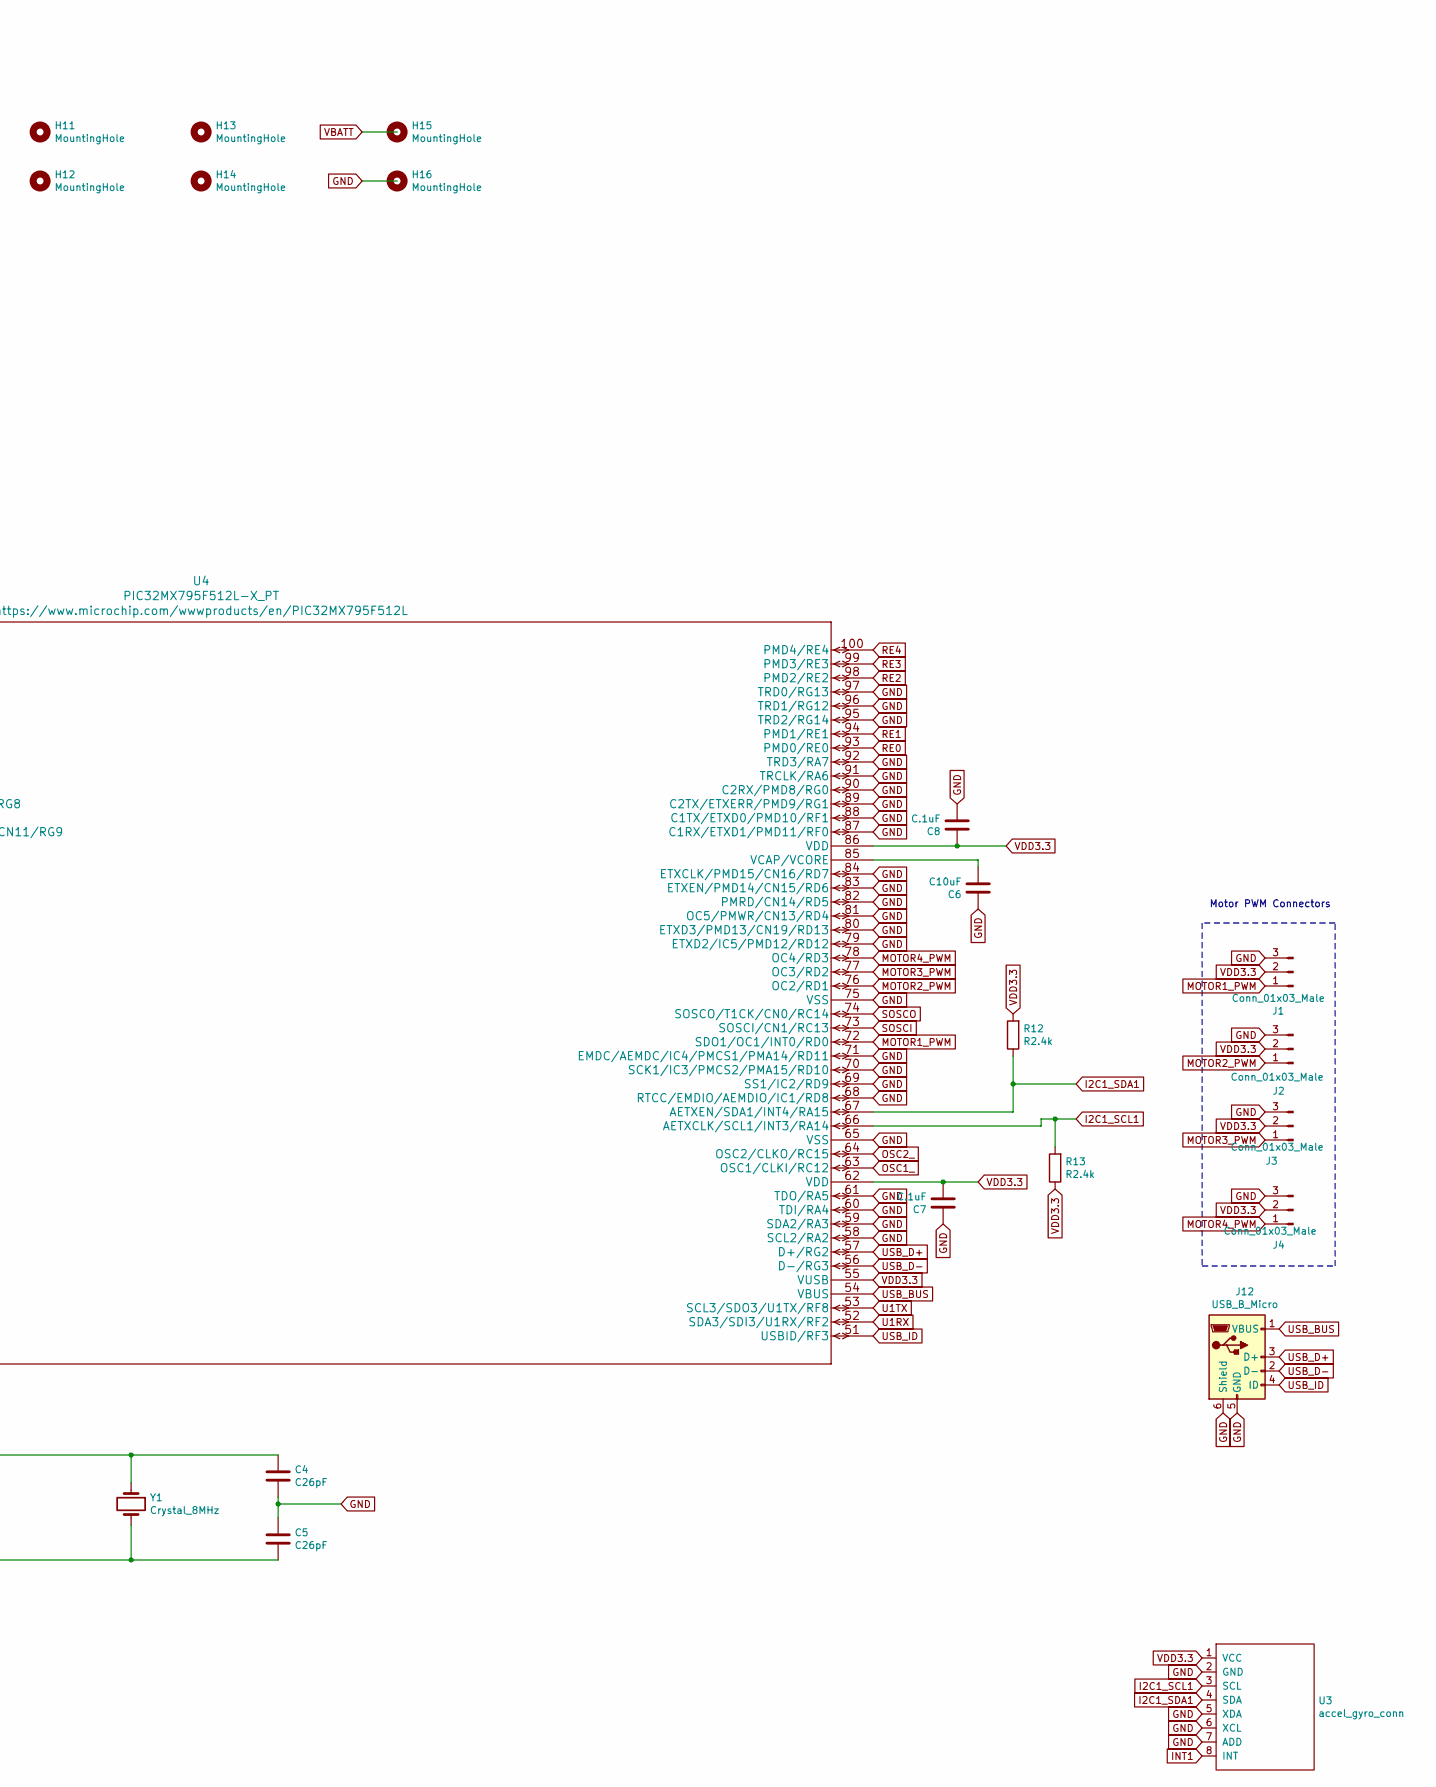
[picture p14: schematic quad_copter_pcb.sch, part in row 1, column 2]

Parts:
C1: C_10uF; C_0805_2012Metric_Pad1.15x1.40mm_HandSolder
C2: C_22uF; C_1206_3216Metric_Pad1.42x1.75mm_HandSolder
C4, C5: C26pF; C_0603_1608Metric_Pad1.05x0.95mm_HandSolder
C6: C10uF; C_0603_1608Metric_Pad1.05x0.95mm_HandSolder
C7, C8, C11, C12, C13: C.1uF; C_0603_1608Metric_Pad1.05x0.95mm_HandSolder
C9, C10: C_.1uF; C_0603_1608Metric_Pad1.05x0.95mm_HandSolder
D1, D2, D3: LED; LED_1206_3216Metric_Pad1.42x1.75mm_HandSolder
H11, H12, H13, H14, H15, H16: MountingHole; MountingHole_3.2mm_M3
J1, J2, J3, J4: Conn_01x03_Male; PinHeader_1x03_P2.54mm_Vertical
J5: Conn_02x05_Odd_Even; PinHeader_2x05_P2.54mm_Vertical
J6: Conn_02x02_Odd_Even; PinHeader_2x02_P2.54mm_Vertical
J8: Conn_02x04_Odd_Even; PinHeader_2x04_P2.54mm_Vertical
J10: Conn_02x03_Odd_Even; PinHeader_2x03_P2.54mm_Vertical
J11: Conn_01x05; PinHeader_1x05_P2.54mm_Vertical
J12: USB_B_Micro; USB_Micro-B_Amphenol_10103594-0001LF_Horizontal
JP1: RJ11-6
JP2: XBEE-LEAVE EMPTY; XBEE
R1, R8, R9: R_56; R_0805_2012Metric_Pad1.15x1.40mm_HandSolder
R2: R10K; R_0805_2012Metric_Pad1.15x1.40mm_HandSolder
R3: R2.8k; R_0805_2012Metric_Pad1.15x1.40mm_HandSolder
R4: R10k; R_0805_2012Metric_Pad1.15x1.40mm_HandSolder
R5: R470; R_0603_1608Metric_Pad1.05x0.95mm_HandSolder
R12, R13: R2.4k; R_0805_2012Metric_Pad1.15x1.40mm_HandSolder
R14: R10; R_0805_2012Metric_Pad1.15x1.40mm_HandSolder
S1: MOMENTARY-SWITCH-SPST-2-SMD-5.2MM; TACTILE_SWITCH_SMD_5.2MM
U1: LT1085-3.3; TO-263-3_TabPin2
U3: accel_gyro_conn; PinSocket_1x08_P2.54mm_Vertical
U4: PIC32MX795F512L-X_PT; TQFP-100_12x12mm_P0.4mm
Y1: Crystal_8MHz; HC49UP

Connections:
AN12: J11.2, U4.41 (AN12/ERXD0/AECRS/PMA11/RB12)
AN13: J11.3, U4.42 (AN13/ERXD1/AECOL/PMA10/RB13)
AN14: J11.4, U4.43 (AN14/ERXD2/AETXD3/PMALH/PMA1/RB14)
AN15: J11.5, U4.44 (AN15/ERXD3/AETXD2/OCFB/PMALL/PMA0/CN12/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)
GND: C1.2, C2.2, C4.2, C5.1, C6.1, C7.1, C8.2, C9.2, C10.1, C11.1, C12.1, C13.1, D1.1 (K), D2.1 (K), D3.1 (K), J1.3, J2.3, J3.3, J4.3, J12.5 (GND), J12.6 (Shield), JP1.3, JP1.6, JP2.10 (GND), R3.2, S1.1, S1.2, U1.1 (GND), U3.2 (GND), U3.5 (XDA), U3.6 (XCL), U3.7 (ADD), U4.1 (AERXERR/RG15), U4.6 (T2CK/RC1), U4.7 (T3CK/RC2), U4.8 (T4CK/RC3), U4.9 (T5CK/SDI1/RC4), U4.15 (VSS), U4.17 (TMS/RA0), U4.20 (AN5/C1IN+/VBUSON/CN7/RB5), U4.21 (AN4/C1IN-/CN6/RB4), U4.23 (AN2/C2IN-/CN4/RB2), U4.26 (PGEC2/AN6/OCFA/RB6), U4.28 (VREF-/CVREF-/AERXD2/PMA7/RA9), U4.29 (VREF+/CVREF+/AERXD3/PMA6/RA10), U4.31 (AVSS), U4.32 (AN8/C1OUT/RB8), U4.33 (AN9/C2OUT/RB9), U4.34 (AN10/CVREFOUT/PMA13/RB10), U4.35 (AN11/ERXERR/AETXERR/PMA12/RB11), U4.36 (VSS), U4.38 (TCK/RA1), U4.39 (AC1TX/SCK4/U5TX/*U2RTS/RF13), U4.40 (AC1RX/*SS4/U5RX/*U2CTS/RF12), U4.45 (VSS), U4.49 (SDA5/SDI4/U2RX/PMA9/CN17/RF4), U4.50 (SCL5/SDO4/U2TX/PMA8/CN18/RF5), U4.58 (SCL2/RA2), U4.59 (SDA2/RA3), U4.60 (TDI/RA4), U4.61 (TDO/RA5), U4.65 (VSS), U4.68 (RTCC/EMDIO/AEMDIO/IC1/RD8), U4.69 (SS1/IC2/RD9), U4.70 (SCK1/IC3/PMCS2/PMA15/RD10), U4.71 (EMDC/AEMDC/IC4/PMCS1/PMA14/RD11), U4.75 (VSS), U4.79 (ETXD2/IC5/PMD12/RD12), U4.80 (ETXD3/PMD13/CN19/RD13), U4.81 (OC5/PMWR/CN13/RD4), U4.82 (PMRD/CN14/RD5), U4.83 (ETXEN/PMD14/CN15/RD6), U4.84 (ETXCLK/PMD15/CN16/RD7), U4.87 (C1RX/ETXD1/PMD11/RF0), U4.88 (C1TX/ETXD0/PMD10/RF1), U4.89 (C2TX/ETXERR/PMD9/RG1), U4.90 (C2RX/PMD8/RG0), U4.91 (TRCLK/RA6), U4.92 (TRD3/RA7), U4.95 (TRD2/RG14), U4.96 (TRD1/RG12), U4.97 (TRD0/RG13)
I2C1_SCL1: J6.3, J6.4, R13.2, U3.3 (SCL), U4.66 (AETXCLK/SCL1/INT3/RA14)
I2C1_SDA1: J6.1, J6.2, R12.1, U3.4 (SDA), U4.67 (AETXEN/SDA1/INT4/RA15)
INT1: U3.8 (INT), U4.18 (AERXD0/INT1/RE8)
MCLR: JP1.1, R5.2, U4.13 (*MCLR)
MOTOR1_PWM: J1.1, U4.72 (SDO1/OC1/INT0/RD0)
MOTOR2_PWM: J2.1, U4.76 (OC2/RD1)
MOTOR3_PWM: J3.1, U4.77 (OC3/RD2)
MOTOR4_PWM: J4.1, U4.78 (OC4/RD3)
unnamed: C6.2, U4.85 (VCAP/VCORE)
unnamed: D1.2 (A), R1.1
unnamed: D2.2 (A), R8.2
unnamed: D3.2 (A), R9.1
unnamed: JP2.6 (RSSI), R8.1
unnamed: JP2.15 (DIO5), R9.2
unnamed: R4.2, S1.3
unnamed: R5.1, S1.4
OSC1_: C5.2, U4.63 (OSC1/CLKI/RC12), Y1.2
OSC2_: C4.1, U4.64 (OSC2/CLKO/RC15), Y1.1
PGC: JP1.5, U4.24 (PGEC1/AN1/CN3/RB1)
PGD: JP1.4, U4.25 (PGED1/AN0/CN2/RB0)
RE0: J8.2, JP2.9 (DTR), U4.93 (PMD0/RE0)
RE1: J8.1, JP2.8 (RES), U4.94 (PMD1/RE1)
RE2: J8.4, JP2.7 (DIO11), U4.98 (PMD2/RE2)
RE3: J8.3, JP2.20 (DIO0), U4.99 (PMD3/RE3)
RE4: J8.6, JP2.14 (RES), U4.100 (PMD4/RE4)
RE5: J8.5, JP2.13 (DIO9), U4.3 (PMD5/RE5)
RE6: J8.8, U4.4 (PMD6/RE6)
RE7: J8.7, U4.5 (PMD7/RE7)
SCK2_SCLK_2: J5.9, J5.10, JP2.18 (DIO2), U4.10 (ECOL/SCK2/U6TX/*U3RTS/PMA5/CN8/RG6)
SDI2_MISO_2: J5.7, J5.8, JP2.4 (DIO12), U4.11 (ECRS/SDA4/SDI2/U3RX/PMA4/CN9/RG7)
SDO2_MOSI_2: J5.5, J5.6, JP2.11 (DIO4), U4.12 (ERXDV/AERXDV/ECRSDV/AECRSDV/SCL4/SDO2/U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)
SOSCI: U4.73 (SOSCI/CN1/RC13)
SOSCO: U4.74 (SOSCO/T1CK/CN0/RC14)
SPI_ATTN_INT_L: J5.1, J5.2, JP2.19 (DIO1), U4.19 (AERXD1/INT2/RE9)
SS2_CSL_2: J5.3, J5.4, JP2.17 (DIO3), U4.14 (ERXCLK/AERXCLK/EREFCLK/AEREFCLK/*SS2/U6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)
U1CTS: J10.1, JP2.16 (RTS), U4.47 (AETXD0/*SS3/U4RX/*U1CTS/CN20/RD14)
U1RTS: J10.3, JP2.12 (CTS), U4.48 (AETXD1/SCK3/U4TX/*U1RTS/CN21/RD15)
U1RX: J10.2, JP2.2 (DOUT), U4.52 (SDA3/SDI3/U1RX/RF2)
U1TX: J10.4, JP2.3 (DIN), U4.53 (SCL3/SDO3/U1TX/RF8)
USB_BUS: J12.1 (VBUS), U4.54 (VBUS)
USB_D+: J12.3 (D+), U4.57 (D+/RG2)
USB_D-: J12.2 (D-), U4.56 (D-/RG3)
USB_ID: J12.4 (ID), U4.51 (USBID/RF3)
VBATT: C1.1, R2.1, U1.3 (VI)
VBATT_SCALED: J11.1, R2.2, R3.1, U4.27 (PGED2/AN7/RB7)
VDD3.3: C2.1, C7.2, C8.1, C9.1, C10.2, C11.2, C12.2, C13.2, J1.2, J2.2, J3.2, J4.2, JP1.2, JP2.1 (VDD), R1.2, R4.1, R12.2, R13.1, R14.1, R14.2, U1.2 (VO), U3.1 (VCC), U4.2 (VDD), U4.16 (VDD), U4.30 (AVDD), U4.37 (VDD), U4.46 (VDD), U4.55 (VUSB), U4.62 (VDD), U4.86 (VDD)
XBEE_RESET: J10.5, JP2.5 (RESET), U4.22 (AN3/C2IN+/CN5/RB3)

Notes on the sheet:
Motor PWM Connectors

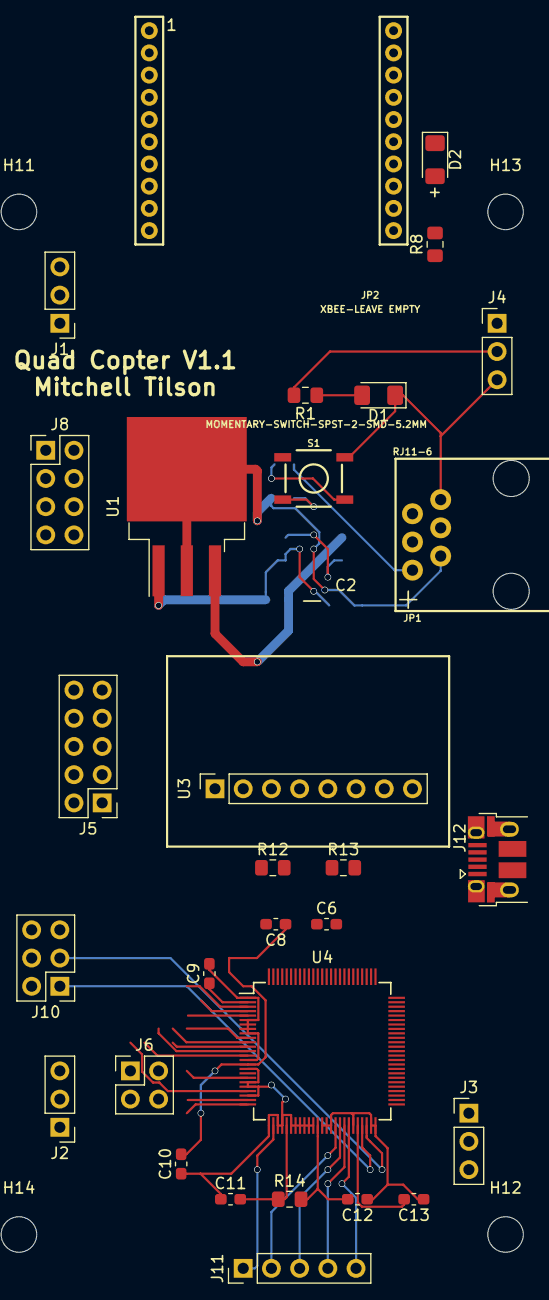
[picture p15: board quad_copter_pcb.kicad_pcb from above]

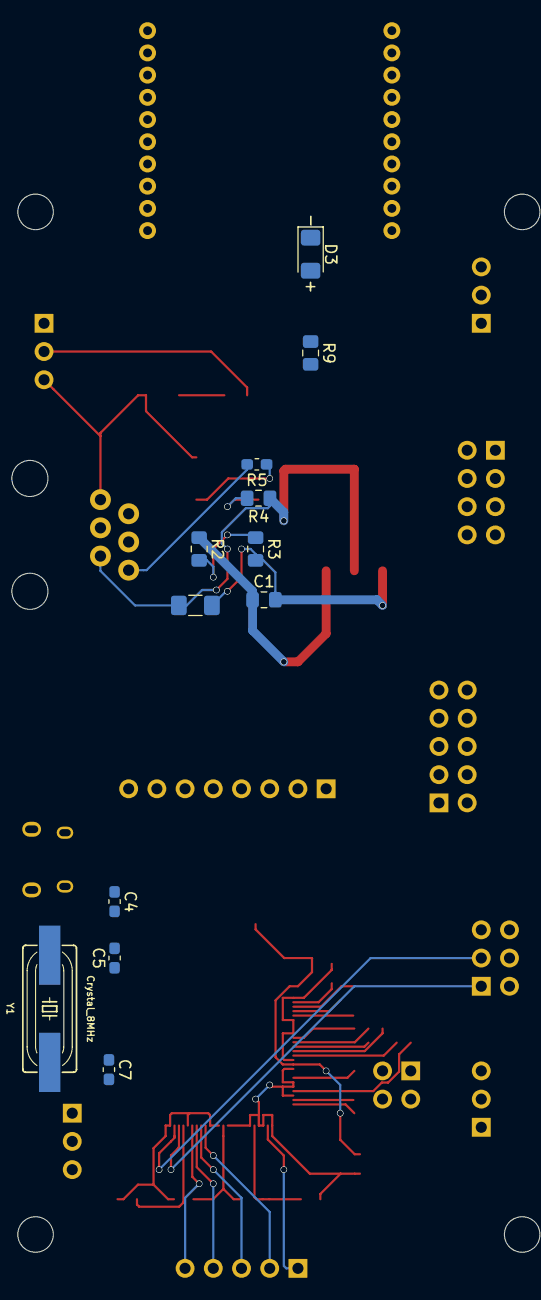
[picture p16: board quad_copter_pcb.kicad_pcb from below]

Board: 2 copper layers, 46 parts (12 on the bottom side), 50 nets.

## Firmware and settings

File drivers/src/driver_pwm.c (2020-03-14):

/*******************************************************************************
 * File:    driver_pwm.c
 * Author:  Mitchell S. Tilson
 * Created: 08/01/2019
 *
 * Description: This file contians the driver interface for the PWM module.
 ******************************************************************************/

/*******************************************************************************
 * Includes
 ******************************************************************************/
#include "driver_pwm.h"
#include <p32xxxx.h>

/*******************************************************************************
 * Local Defines
 ******************************************************************************/
#define PWM_MODE_NO_FAULT_DETECTION (6)

/*******************************************************************************
 * Local Type Defs
 ******************************************************************************/
typedef struct {
    volatile __OC1CONbits_t* OCxCON;
    volatile uint32_t* OCxRS;
    volatile uint32_t* OCxR;
    bool initialized;
} pwm_config_t;

/*******************************************************************************
 * Local Data
 ******************************************************************************/
pwm_config_t PWM1_cfg = {
    &OC1CONbits,
    &OC1RS,
    &OC1R,
    false,
};

pwm_config_t PWM2_cfg = {
    /*
     * This cast seems dangerous, but is ok given the registers
     * are all defined the same way.
     */
    (__OC1CONbits_t*)&OC2CONbits,
    &OC2RS,
    &OC2R,
    false,
};

pwm_config_t PWM3_cfg = {
    (__OC1CONbits_t*)&OC3CONbits,
    &OC3RS,
    &OC3R,
    false,
};

pwm_config_t PWM4_cfg = {
    (__OC1CONbits_t*)&OC4CONbits,
    &OC4RS,
    &OC4R,
    false,
};

static bool pwm_tmr_initialized = false;

pwm_config_t* curr_pwm_cfg_p;

/*******************************************************************************
 * Local Functions
 ******************************************************************************/
static int32_t pwm_set_cfg_pointer( pwm_num_e pwm );

/*******************************************************************************
 * Public function section
 ******************************************************************************/

/*******************************************************************************
 * PWM_init_tmr
 *
 * Description: Initializes the PWM timer
 *
 * Inputs:      uint32_t period - periodicity of the pulse
 *
 * Returns:     None
 *
 * Revision:    Initial Creation 02/16/2019 - Mitchell S. Tilson
 *
 * Notes:       The clock is set up for 80MHz and the prescale value is set to 256.
 *
 ******************************************************************************/
void PWM_init_tmr( uint32_t period )
{
    // Set up the period
    PR2 = period;

    // Set the timer prescale value
    // TCKPS<2:0>: Timer Input Clock Prescale Select bits
    // 111 = 1:256 prescale value
    // 110 = 1:64 prescale value
    // 101 = 1:32 prescale value
    // 100 = 1:16 prescale value
    // 011 = 1:8 prescale value
    // 010 = 1:4 prescale value
    // 001 = 1:2 prescale value
    T2CONbits.TCKPS = 6;

    // Clear timer 2
    TMR2 = 0;

    pwm_tmr_initialized = true;
}

/*******************************************************************************
 * PWM_init (call PWM_init_tmr first)
 *
 * Description: Initializes the PWM identified by the pwm_num_e using the passed
 *              pwm_init_t settings. (call PWM_init_tmr first)
 *
 * Inputs:      pwm_num_e pwm - the pwm to initialize
 *              pwm_init_t init_settings:
 *                  uint32_t period - periodicity of the pulse
 *                  uint32_t duty - duty cycle
 *
 * Returns:     None
 *
 * Revision:    Initial Creation 08/01/2019 - Mitchell S. Tilson
 *
 * Notes:       The clock is set up for 80MHz and the prescale value is set to 256.
 *              For a 16bit timer, this means the slowest period is (1/80e6)*65535*64 = 0.052428
 *              The period can be calculated as perod_s = (1/80e6)*(init_settings.period)*256.
 *              (call PWM_init_tmr first)
 *
 ******************************************************************************/
void PWM_init( pwm_num_e pwm, pwm_init_t init_settings )
{
    if( -1 == pwm_set_cfg_pointer( pwm ) )
    {
        return;
    }

    if( pwm_tmr_initialized == false )
    {
        return;
    }

    // Set the intialized flag
    curr_pwm_cfg_p->initialized = false;

    // Can't be greater than 2^16 - 1
    if( init_settings.period > 65535 )
    {
        return;
    }

    // Disable the PWM module
    curr_pwm_cfg_p->OCxCON->ON = 0;
    __asm__("nop");

    // Set up the duty cycle
    float percentage = (float)init_settings.duty/100.0;
    float clk_val = ((float)init_settings.period)*percentage;
    *curr_pwm_cfg_p->OCxRS = (uint32_t)(clk_val + 0.5);
    *curr_pwm_cfg_p->OCxR = *curr_pwm_cfg_p->OCxRS;
    curr_pwm_cfg_p->OCxCON->OCM = PWM_MODE_NO_FAULT_DETECTION;

    // Set the intialized flag
    curr_pwm_cfg_p->initialized = true;
}

/*******************************************************************************
 * PWM_tmr_en
 *
 * Description: Enables or disables Timer 2
 *
 * Inputs:      bool en - enable (true) or disable (false) timer 2
 *
 * Returns:     None
 *
 * Revision:    Initial Creation 02/16/2019 - Mitchell S. Tilson
 *
 * Notes:
 *
 ******************************************************************************/
void PWM_tmr_en( bool en )
{
    if( pwm_tmr_initialized )
    {
        T2CONbits.ON = en;
        __asm__("nop");
    }
}

/*******************************************************************************
 * PWM_start
 *
 * Description: Starts the selected PWM
 *
 * Inputs:      pwm_num_e pwm - the pwm start
 *
 * Returns:     None
 *
 * Revision:    Initial Creation 01/25/2016 - Mitchell S. Tilson
 *
 *              02/14/2016 - chech intialization.
 *              02/16/2019 - Timer 2 is used for all PWMs
 *
 * Notes:
 *
 ******************************************************************************/
void PWM_start( pwm_num_e pwm )
{
    if( -1 == pwm_set_cfg_pointer( pwm ) )
    {
        return;
    }

    if( !curr_pwm_cfg_p->initialized )
    {
        return;
    }

    // Enable the pwm
    curr_pwm_cfg_p->OCxCON->ON = 1;
    __asm__("nop");
}
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

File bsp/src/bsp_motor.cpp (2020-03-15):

/*******************************************************************************
 * File:    bsp_motor.cpp
 * Author:  Mitchell S. Tilson
 * Created: 03/01/2019
 *
 * Description: This file provides the motor control class
 *
 ******************************************************************************/

/*******************************************************************************
 * Includes
 ******************************************************************************/
#include "bsp_motor.h"
#include "cfg.h"

/*******************************************************************************
 * Private data
 ******************************************************************************/
#define LOW_PWM_DUTY_CYCLE (50.0)
#define MAX_PWM_DUTY_CYCLE (95.0)

const pwm_init_t BSPMotor::pwm_init_data = {
    // (1/80e6)*313*64 = 0.0002504s ~250us
    .period = 313,
#if DO_THROTTLE_CAL == 1
    .duty = MAX_PWM_DUTY_CYCLE,
#else
    .duty = LOW_PWM_DUTY_CYCLE,
#endif
};

/*******************************************************************************
 * Public Method Section
 ******************************************************************************/

/*******************************************************************************
 * BSPMotor
 *
 * Description: Class constructor function
 *
 * Inputs:      None
 *
 * Returns:     None
 *
 * Revision:    Initial Creation 03/01/2019 - Mitchell S. Tilson
 *
 ******************************************************************************/
BSPMotor::BSPMotor( void )
{
}

/*******************************************************************************
 * static InitTmr
 *
 * Description: Initializes the timer
 *
 * Inputs:      None
 *
 * Returns:     None
 *
 * Revision:    Initial Creation 03/01/2019 - Mitchell S. Tilson
 *
 ******************************************************************************/
void BSPMotor::InitTmr( void )
{
    // Initialize the timer
    PWM_init_tmr( pwm_init_data.period );
}

/*******************************************************************************
 * Init
 *
 * Description: Initializes a motor
 *
 * Inputs:      pwm_num_e pwm - The PWM assigned to this object
 *
 * Returns:     None
 *
 * Revision:    Initial Creation 03/01/2019 - Mitchell S. Tilson
 *
 ******************************************************************************/
void BSPMotor::Init( pwm_num_e pwm )
{
    _pwm = pwm;
    PWM_init( _pwm, pwm_init_data );
}

/*******************************************************************************
 * TmrEn
 *
 * Description: Enables Timer2
 *
 * Inputs:      None
 *
 * Returns:     None
 *
 * Revision:    Initial Creation 03/01/2019 - Mitchell S. Tilson
 *
 ******************************************************************************/
void BSPMotor::TmrEn( void )
{
    PWM_tmr_en( true );
}

/*******************************************************************************
 * Start
 *
 * Description: Starts a given motor
 *
 * Inputs:      None
 *
 * Returns:     None
 *
 * Revision:    Initial Creation 03/01/2019 - Mitchell S. Tilson
 *
 ******************************************************************************/
void BSPMotor::Start( void )
{
    PWM_start( _pwm );
}

/*******************************************************************************
 * SetSpeedPercent
 *
 * Description: Sets the speed of a motor
 *
 * Inputs:      float speed the speed in percentage (0 to 100%)
 *
 * Returns:     None
 *
 * Revision:    Initial Creation 03/01/2019 - Mitchell S. Tilson
 *
 ******************************************************************************/
void BSPMotor::SetSpeedPercent( float speed )
{
    float pwm_duty_cycle = (MAX_PWM_DUTY_CYCLE - LOW_PWM_DUTY_CYCLE)*speed + LOW_PWM_DUTY_CYCLE;
    PWM_chg_duty( _pwm, pwm_duty_cycle );
}

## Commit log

2014-09-03 Update call to Uart_write to not pass 'TRUE' or 'FALSE'. All writes are blocking for now.
2016-01-23 Build system fixed. This will now build without the use of the MPLAB IDE
    [cpu_core.h]
2016-01-25 Update the Makefile to generate a map file and start printing the accel device ID
2016-01-25 Start of the pwm drivers
2016-01-25 Update the PWM drivers to have start and stop functionality
2016-01-26 PWM updates to allow duty cycle changes on the fly and some test code in button reader
2016-02-09 Update to use 256 as the PWM pre-scale value
2016-02-15 Check to ensure PWM is initialized prior to make any changes and fix some whie space stuff
    [driver_pwm.c]
2016-02-16 Fixed comments in PWM driver and added the start of the SPI driver
    [driver_pwm.c, driver_spi.c, driver_spi.h]
2016-02-17 Changes to get SPI driver compiling for now
2016-03-07 Updates for spi interupts
2016-03-07 Fix interrupt flag register
    [driver_spi.c]
2016-03-07 Fix interrupt flag register for real this time
    [driver_spi.c]
2016-03-07 More interrupt fixes
2018-11-21 Playing around with the ESC.
2018-11-23 Testing the accel gyro again and adding the python plotting utility for the accel gyro
2018-11-24 Fixing some printf issues and attempting to run at a higher rate
    [bsp_utils.c]
2018-11-25 Initial PCB
    [_saved_quad_copter_pcb.sch, quad_copter_pcb.kicad_pcb, quad_copter_pcb.sch]
2018-12-10 Add the PCB
    [Sample-BOM-format.xls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]
2018-12-10 Few more PCB files
    [_saved_quad_copter_pcb.sch, quad_copter_pcb4.csv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]
2018-12-21 PCB changes
    [_saved_quad_copter_pcb.sch, quad_copter_pcb.kicad_pcb, quad_copter_pcb.xls]
2018-12-23 The start of cleaning up the accel gyro code (MPU6050)
2019-01-07 Update the schematic stuffs
    [_saved_quad_copter_pcb.sch]
2019-01-07 small changes for SPI and Xbee
2019-01-08 Doesn't build: Added xbee init code
    [driver_spi.h, hal_xbee.c]
2019-01-19 One step closer to an xbee comm layer (added a semaphore call back structure)
    [_saved_quad_copter_pcb.sch]
2019-01-22 Printf now uses comms_xbee layer
2019-01-27 Try to enable interrupts for the MPU6050 (accel_gyro)
2019-01-28 Currently runs but dies after a bit. Probably a buffer overrun.
2019-01-29 Craps out after a few seconds currently
2019-01-31 Rando fixes for things
    [bsp_accel_gyro.cpp, bsp_utils.c, comms_xbee.c]
2019-02-01 Removed accel gyro interrupt. It was too noisy. Polling for now.
2019-02-04 Attempting to calculate roll and pitch
2019-02-06 Functioning example for calculating roll and pitch
2019-02-09 A few compile time bugs squashed
    [comms_xbee.c]
2019-02-11 Trying to get interrupts working
2019-02-11 Use a single handler for all interrupts
2019-02-12 Enable deferred ISR in the OS. Seems to fix interrupts
    [bsp_xbee.c, comms_xbee.c]
2019-02-13 Something to test! (adds in algorithm, maybe app code, for reading accel and outputing PWM values)
2019-02-14 Update alg_stabilizer to be c++ and fix some compile errors
    [alg_stabilizer.cpp]
2019-02-16 Broken pwm push
2019-02-17 Update to enable all PWMs and rename PWM0 to PWM1 just to fit the motor names
2019-02-18 It would be driving all 4 motors if I hadn't blown one of them
    [alg_stabilizer.cpp, driver_pwm.c]
2019-02-18 Work around for OC3 being broken
    [driver_pwm.c]
2019-02-18 Work around doesn't work, but I think its confusing the Os
    [alg_stabilizer.cpp, driver_pwm.c, driver_pwm.h]
2019-02-23 Use compiler interrupts and use single compare continuous toggle and interrupts for TMR2 and OC3
2019-03-02 Minor chagnes to use RE1 instead of RE6 for the broken PWM
    [driver_pwm.c]
2019-03-02 Use objects for the BSP level motor control
2019-03-02 Start to setup for RX message handling. Next step is to use it for changing the motor speed
2019-03-03 First iteration on actually calculating motor speeds
2019-04-14 Enhancements for communication and fixes for the serial buffer reader
    [alg_stabilizer.cpp, bsp_xbee.c, comms_xbee.c]
2019-04-20 Add filter and change messages. This will need to be merged with what is at home
2019-04-24 Start throttle at zero
2019-04-25 Increase P and I constants for the controller. Last time it didn't respond fast enough and we rolled
    [alg_stabilizer.cpp]
2019-04-25 Updating testing python scripts to be threaded
2019-04-27 Set fail safe for the throttle and update the test script
    [alg_stabilizer.cpp]
2019-04-27 Fix compile time error
    [alg_stabilizer.cpp]
2019-04-27 Constant update and better fail safe
    [alg_stabilizer.cpp]
2019-06-02 Add battery voltage tracking.
2019-06-17 One step closer to having a calibration section of flash
2019-06-17 Add in the ability to calibrate the accel gyro on demand and store it in flash
2019-06-18 Add calibration for real
2019-06-20 Closer to having the ability to save calibration to flash
2019-06-21 Saving calibration to flash is now working
2019-06-24 Track how how often the accel/gyro produces a sample
2019-06-25 Work around accidentally cutting RE1 too much by using RE6
    [alg_stabilizer.cpp, driver_pwm.c]
2019-06-25 Attempt to calibrate the motors
2019-06-26 Throttle cal and filter choice change in MPU6050
2019-06-26 Up the data rate to 200Hz and change how the euler angles are calcualted
2019-06-26 Revert changes to calculations of the angles for now
    [alg_stabilizer.cpp]
2019-07-01 Back on ubuntu and adding some stability updates
    [alg_stabilizer.cpp, bsp_accel_gyro.cpp]
2019-07-07 Add in the ability to set the pitch,roll, and yaw. Yaw not supported by controller yet
2019-07-07 Send battery voltages again
2019-07-13 Attempting to tune...
    [quad_copter_pcb.sch]
2020-02-02 PCB updates
    [qc_pcb.dsn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]
2020-02-02 More fixing the comms
    [bsp_xbee.c, comms_xbee.c]
2020-03-14 Update the drivers
2020-03-14 Clean up battery reading
